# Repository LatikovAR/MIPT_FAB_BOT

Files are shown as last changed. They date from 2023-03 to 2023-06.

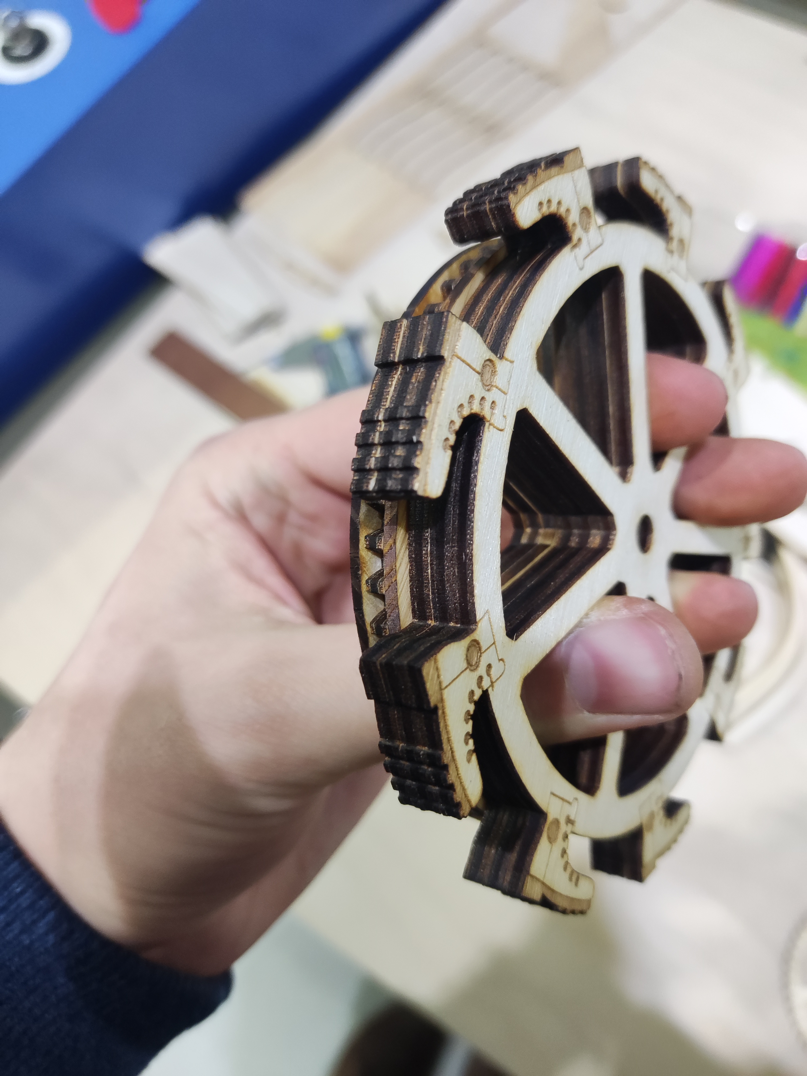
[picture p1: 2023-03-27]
Photo/laser1.jpg

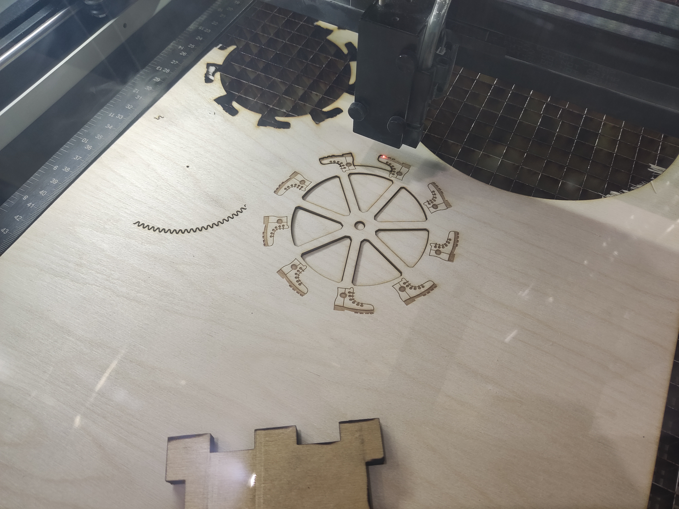
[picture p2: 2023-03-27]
Photo/laser0.jpg

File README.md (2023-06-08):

# MIPT_FAB_BOT

# Задача

Разработать передвигающегося робота для преодоления полосы препятствий, включающей (в порядке прохождения):
* Бассейн с зефирками
* Эстакаду
* Проезд по тунелю, выход из которого открывается светом
* Лопанье шарика.

Робот не должен быть гусеничным или иметь *абсолютно* круглые колеса. Приветствуется сделать максимально интересного робота.

# Решение

Шагающие машины, несмотря на их интересность, были отвергнуты из-за их сложности в изготовлении и отсутствие гарантии успешного решения задачи в условиях ограниченного времени.

В ходе планирования КБ "Инвалид" было принято реализовать классическую, надежную как швейцарские часы схему с полным приводом, двумя двигателями (по одному на 2 колеса каждой стороны) и жестко закрепленными колесами - поворот осуществляется разностью скоростей на правой и левой стороне.

engines

Для преодоления бассейна требовалась большая устойчивость и проходимость. Поэтому центр тяжести был опущен переносом аккумуляторов под днище и установкой больших колес для увеличения дорожного просвета, передаточное отношение двигатель-колесо 1:3.

Колеса из нескольких слоев 3мм фанеры с сапогами на ободе, отсюда одно из рабочих названий - "Пошло поехало". В роли полуосей выступают болты М5. Слоеное колесо зажимается гайками на полуоси. Крепление колес к кузову напечатано на 3D принтере, полуоси в нем фиксируются контргайками так, чтобы свободно вращаться.

Ведомые шестерни располагаются на колесах и зажаты дисками с обеих сторон. Диски фиксируют ведущую шестерню и исключают ее боковые перемещения. Ведущая шестерня вообще говоря может перемещаться по валу двигателя, но держится плотно.

wheels

Для увеличения жесткости, кузов сделан двухслойным, верхний слой стоит на стойках на расстоянии от днища. Напечатать стойки не получилось, они были заменены на набор вырезанных из фанеры шайб.

stoyka

Для открытия туннеля были реализованы огни на светодиодных лентах. А именно: автоматические поворотники и тормозные огни, габариты, включающиеся с пульта фары.

Пульт был собран на макетной плате, без корпуса. Управление осуществлялось двумя джойстиками, каждый управлял "газом" со своей стороны. Нажатия на джойстики активировали фары и пушку.



Пробитие шарика осуществлялось пушкой. Конструкция основана на таковой у страйкбольных приводов: шестерня с отсутствующими зубьями оттягивает подрезиненную рейку пока зубья не закончатся, после чего рейка отстреливает. На конце рейки закреплено лезвие. В результате испытаний оказалось что PLA не выдерживает таких ударных нагрузок, рейку разрывает и ее кусок отстреливает вместе с лезвием, что добавляет эффектности и поражающей способности. Поэтому рейка была склеена для единственного реального выстрела, с чем справилась.

Крепилась пушка стяжкой из-за нехватки времени. На случай отказа к передней части робота была прикреплена спица из проволоки.

bfg

knife

# Оборудование и материалы
* Arduino UNO x2 - пульт и "мозги" машины
* Сервопривод постоянного вращения FS5103R - привод шестерни пушки
* Коллекторные двигатели x2 - привод колес
* Motor shield - подключение коллекторных двигателей
* 2x 18650 с блоком - питание
* Адресная светодиодная лента WS281X - огни
* Радио модуль NRF24L01 - передача и прием сигнала
* 3D принтер Creality Ender-3 S1 Pro + PLA - печать креплений колес и двигателей, пушки
* GCC Laser Pro Spirit GLS 4.10 - лазерная резка 3мм фанеры: колеса и корпус.
* Болты M5 - полуоси
* Болты M3x8, M3x50 - крепление двигателей, корпуса, аккумуляторного блока, сборка пушки.

* Freecad, Solidworks - проектирование деталей под 3D печать
* CorelDraw, Inkscape - проектирование деталей под лазерную резку.

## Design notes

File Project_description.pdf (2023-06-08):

# Квадрокоптер своими руками

### Команда: Титов Егор Михайлович Латиков Александр Романович

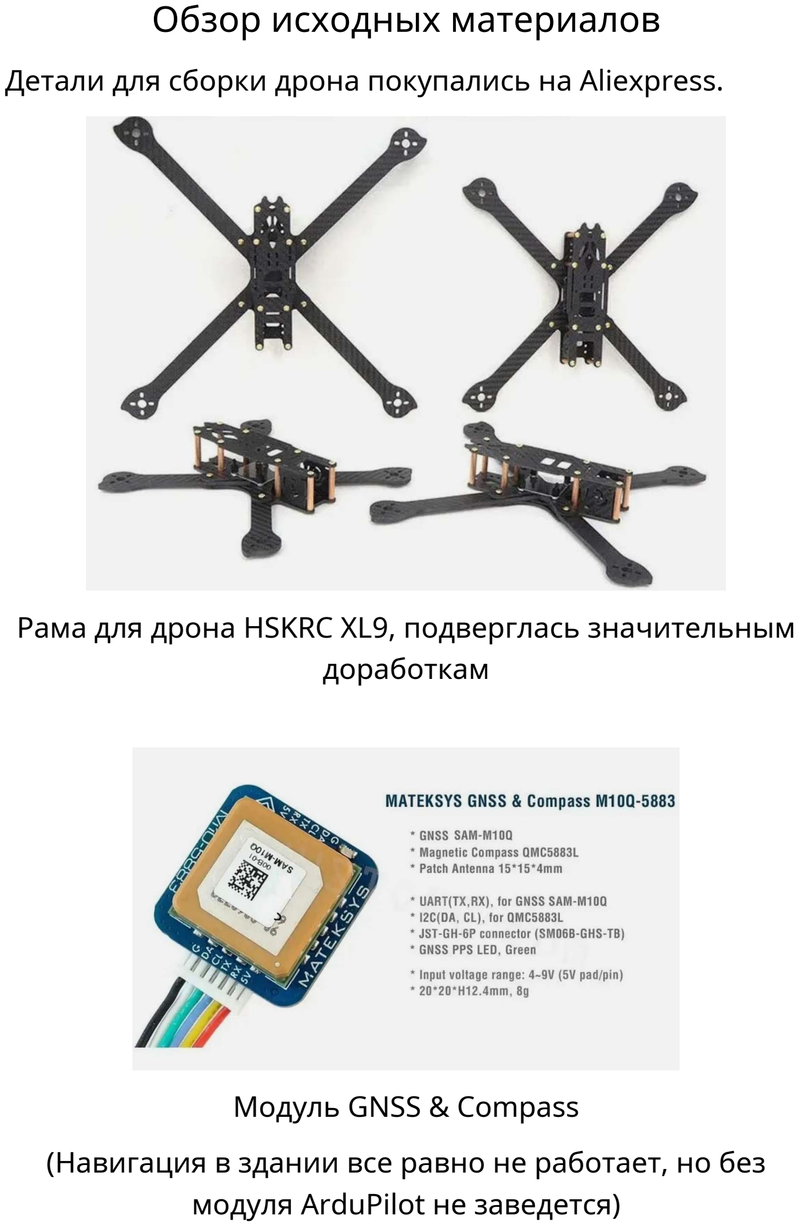
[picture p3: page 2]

### Обзор исходных материалов

Детали для сборки дрона покупались на Aliexpress.

Рама для дрона HSKRC XL9, подверглась значительным доработкам

Модуль GNSS & Compass
(Навигация в здании все равно не работает, но без модуля ArduPilot не заведется)

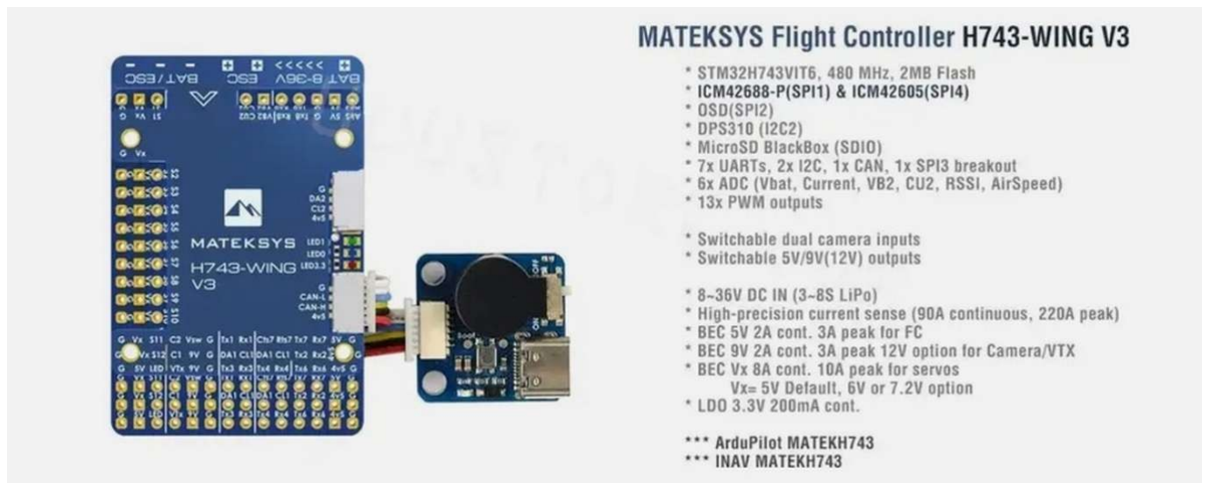
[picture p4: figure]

Полетный контроллер с программатором

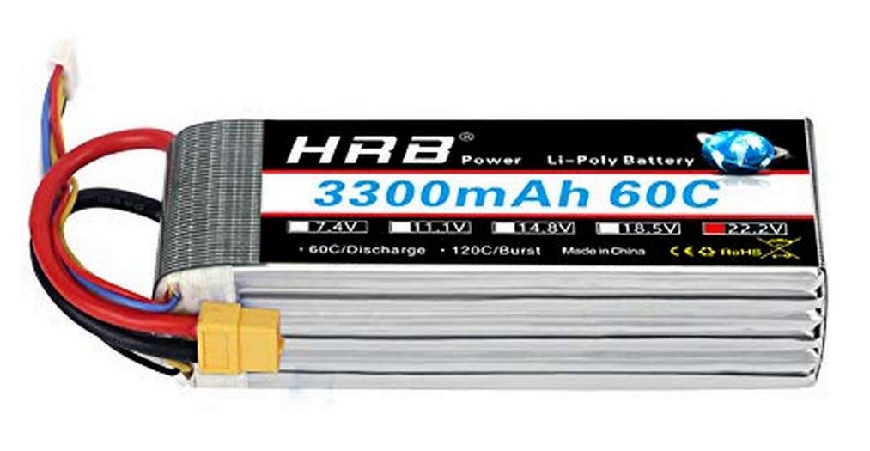
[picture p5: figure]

Аккумулятор HRB Lipo 4S 3300mah 60C XT60

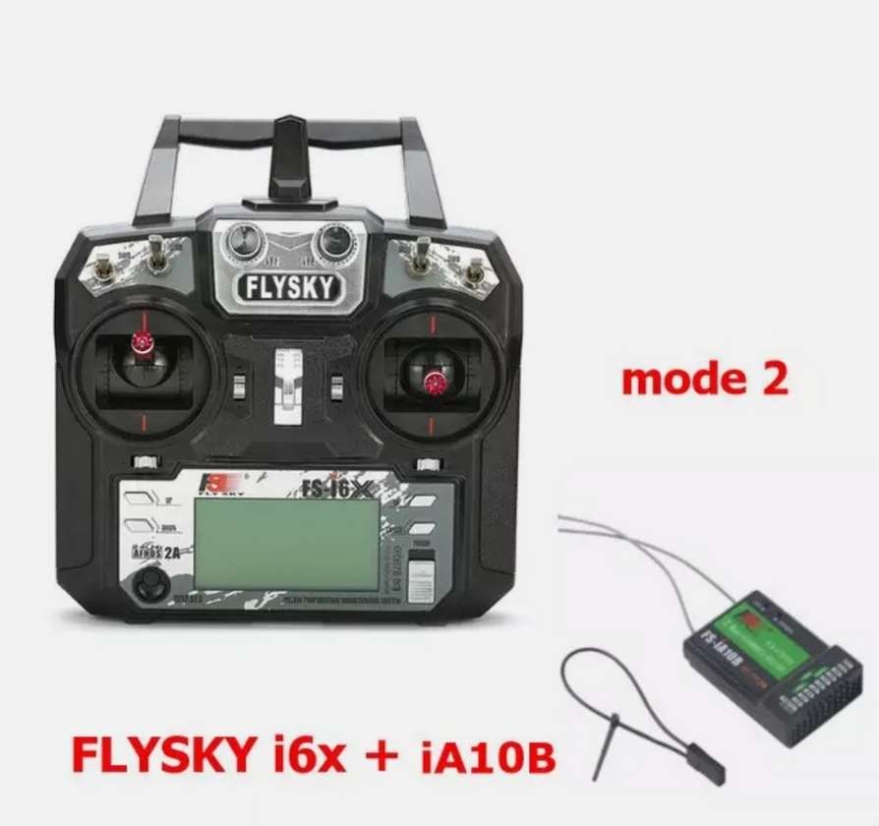
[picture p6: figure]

Передатчик + приемник управляющего сигнала Передатчик 10-канальный, на 2,4 ГГц Приемник 6-канальный, на 2,4 ГГц

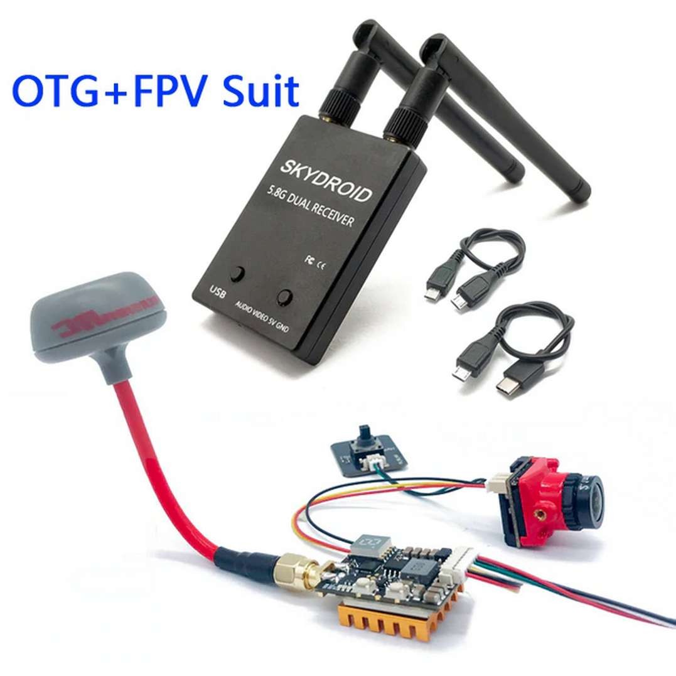
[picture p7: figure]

FPV система
аналоговая камера
передатчик + приемник 5.8 ГГц

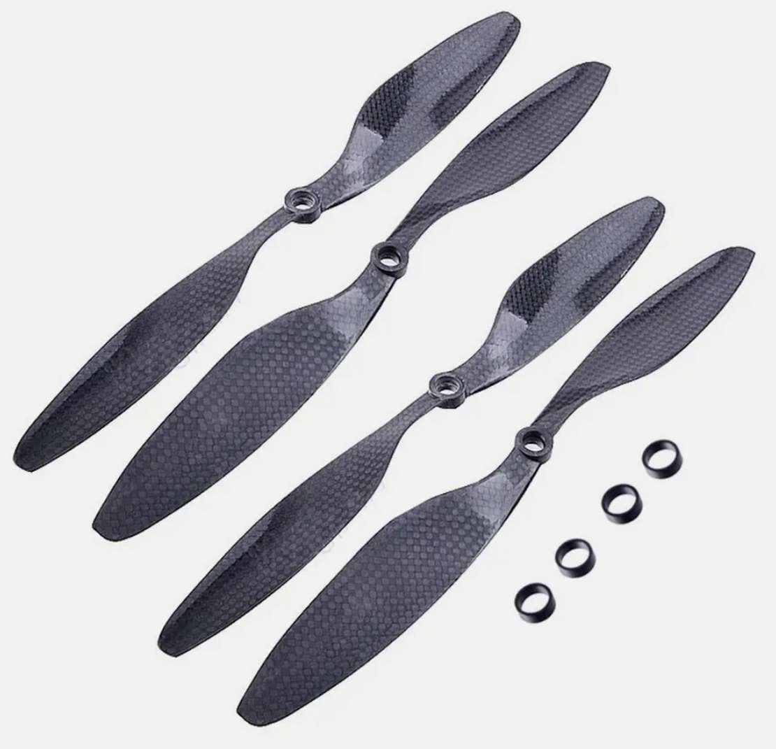
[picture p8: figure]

Комплект пропеллеров 1

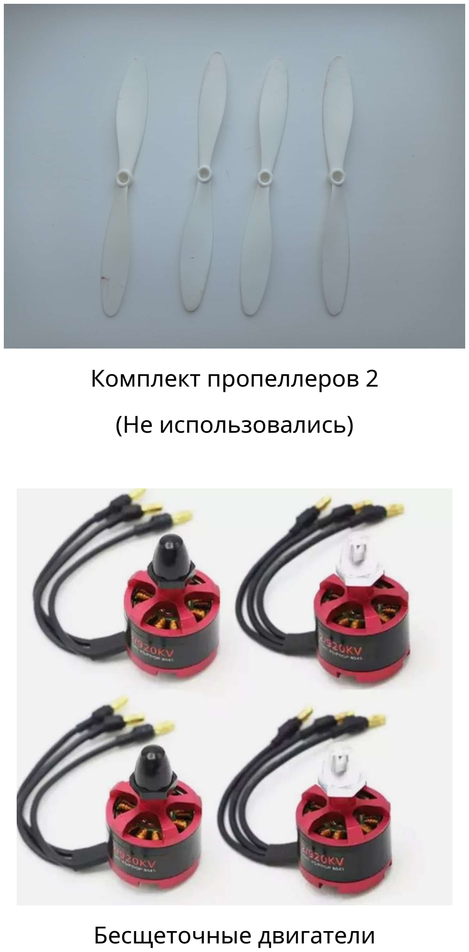
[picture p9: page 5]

Комплект пропеллеров 2
(Не использовались)

Бесщеточные двигатели

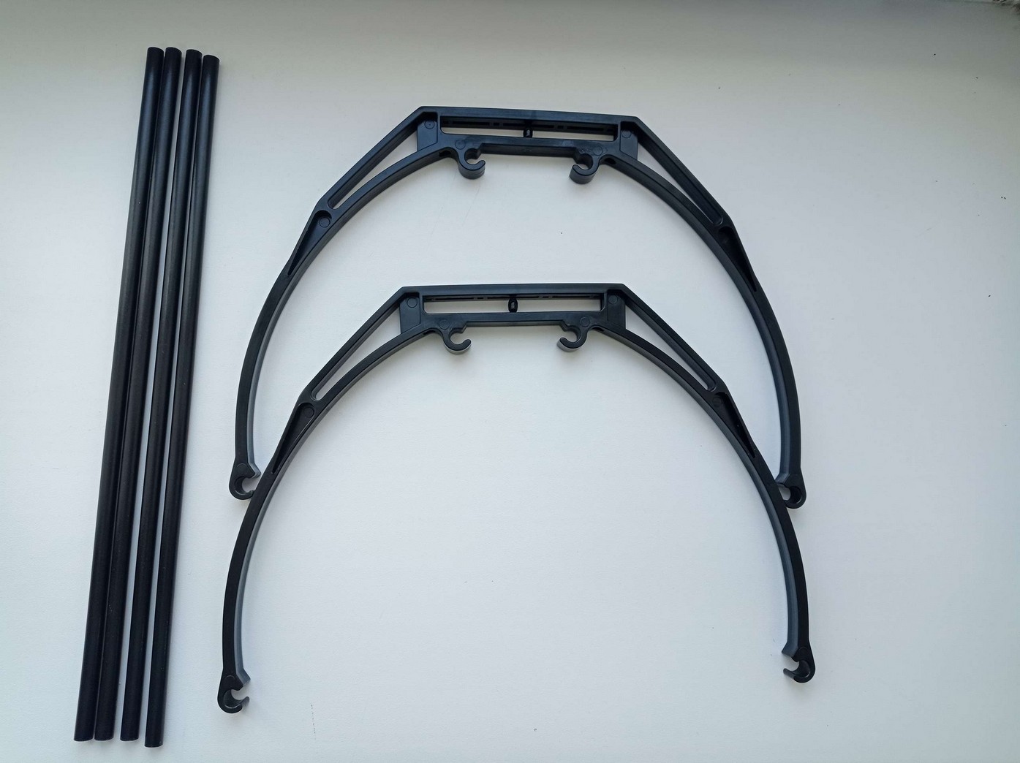
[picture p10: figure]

Шасси
(Использовались только углепластиковые трубки)

### Держатель для камеры

В комплекте рамы были приспособления для закрепления камеры.

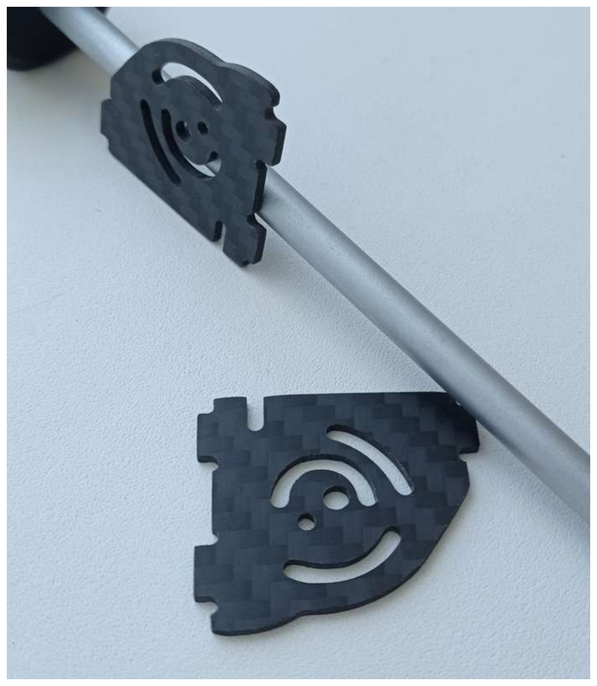
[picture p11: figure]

Однако в силу своей геометрии они не подходили к нашей камере. Поэтому для них была сделана замена:

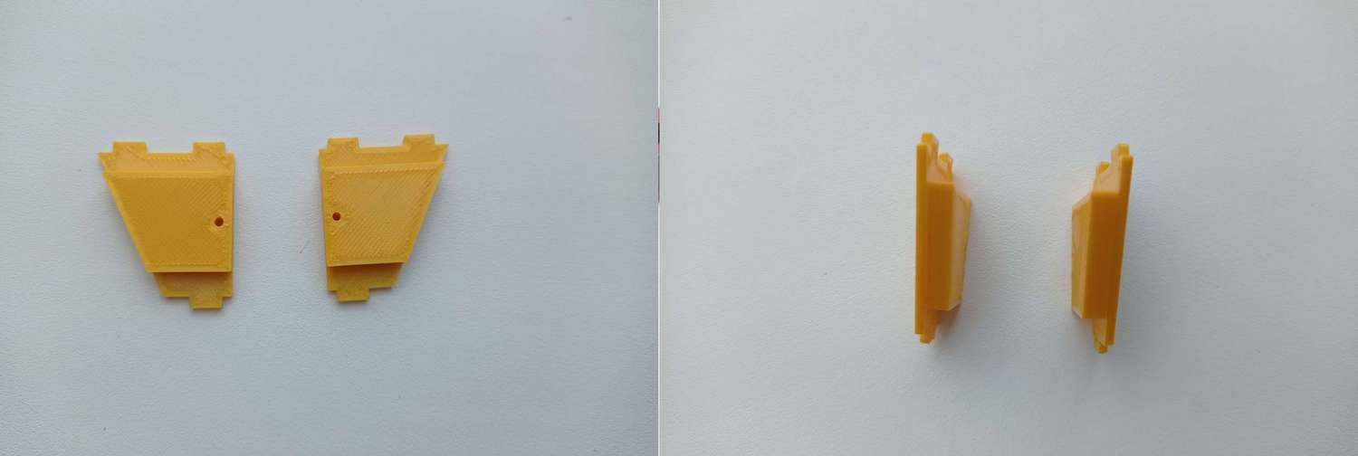
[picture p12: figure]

### Стойки для антенн

Для закрепления антенн приема управляющего сигнала, передачи видеоизображения и антенны GNSS были изготовлены стойки. При их разработке ставилась задача максимально возможного удаления антенн друг от друга для снижения возможного взаимного влияния.

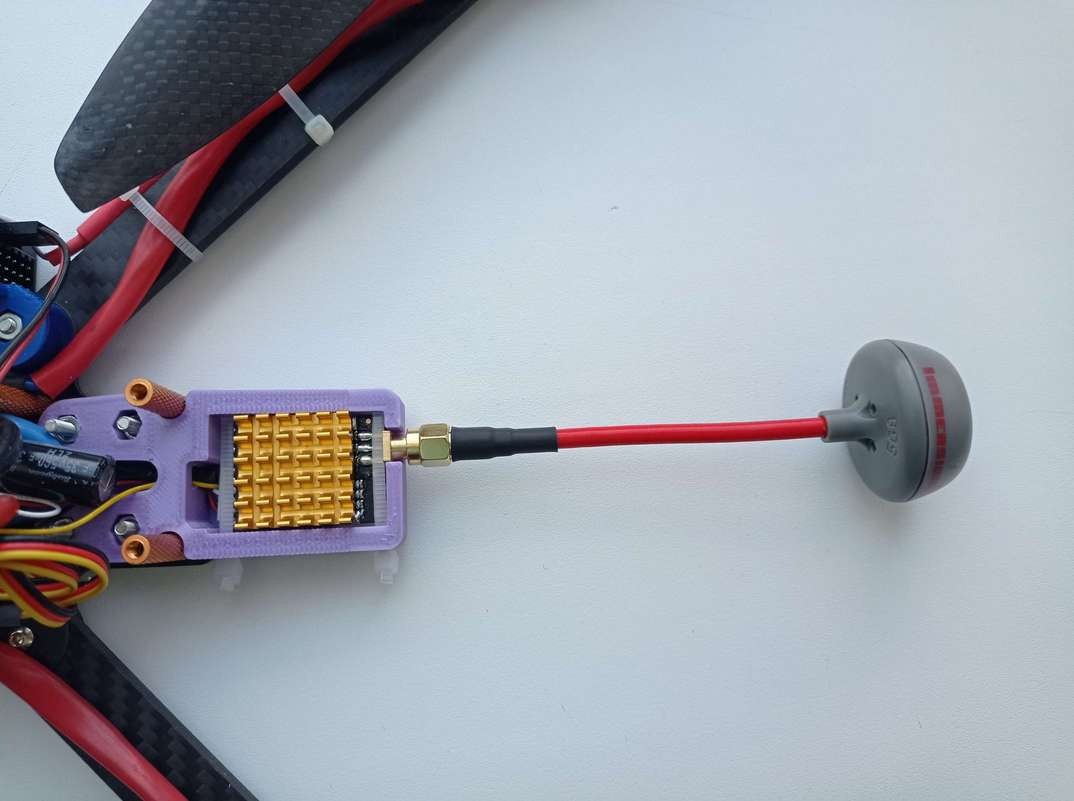
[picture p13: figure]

Передатчик видеоизображения

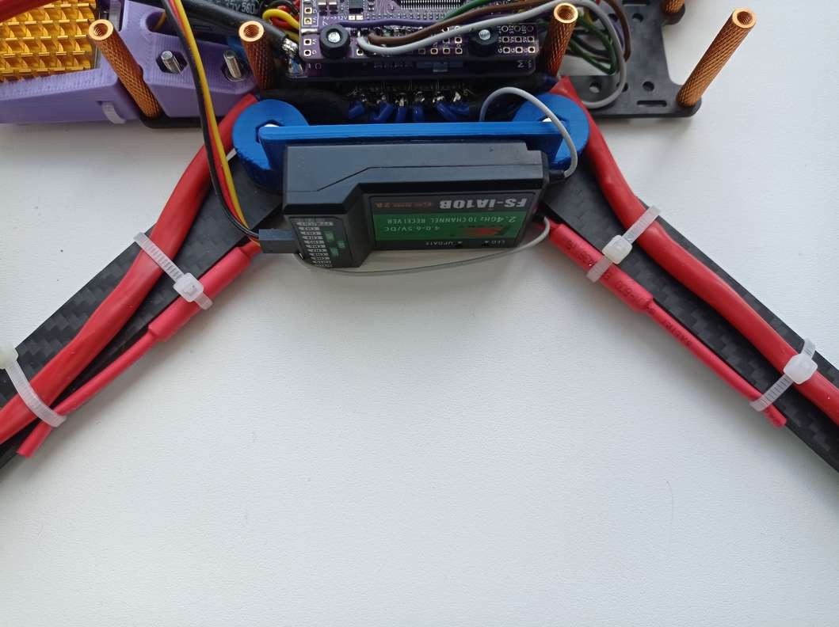
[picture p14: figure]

Приемник управляющего сигнала (Сами антенны закреплены стяжками на раму)

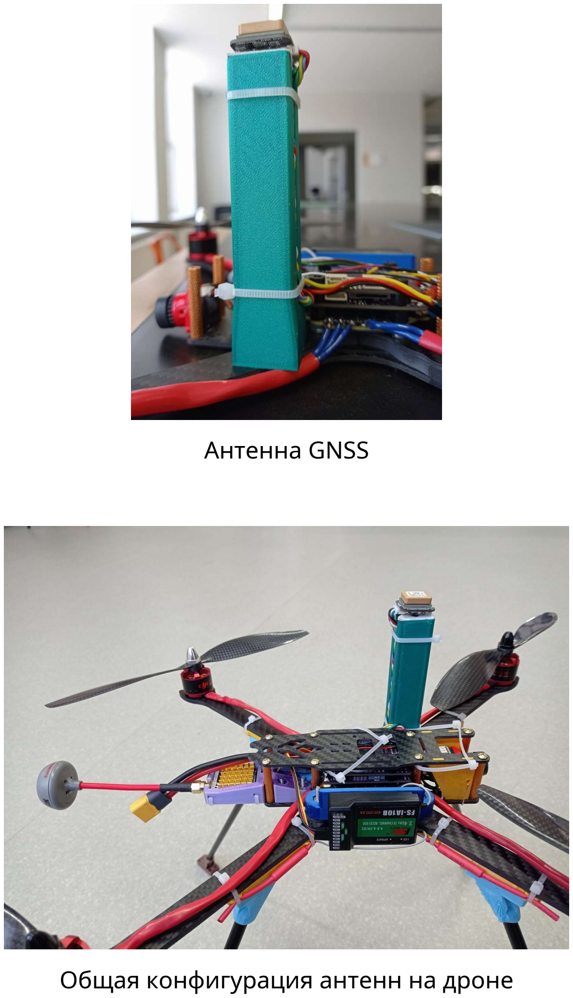
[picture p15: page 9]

Антенна GNSS

Общая конфигурация антенн на дроне

### Сопряжение лопастей и двигателей

Имеющиеся двигатели и лопасти не подходили друг к другу. Большой проблемой было то, что диаметр отверстия лопасти был больше диаметра вала двигателя на ~0.2мм. Сделать втулку под такие размеры крайне проблематично. После исследования различных вариантов для ликвидации зазора была выбрана термоусадка. Процесс установки лопастей является относительно трудоемким для повторения и не был отснят, поэтому подробной фотографии нет.

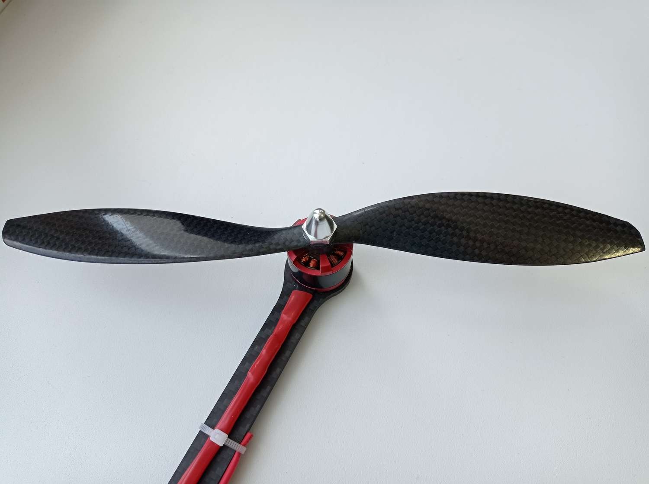
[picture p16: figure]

### Разводка и пайка электроники

Довольно трудоемким был процесс разводки и пайки проводов для соединения компонентов между собой. Основную сложность составляли очень ограниченные размеры и геометрия, диктуемые рамой беспилотника.

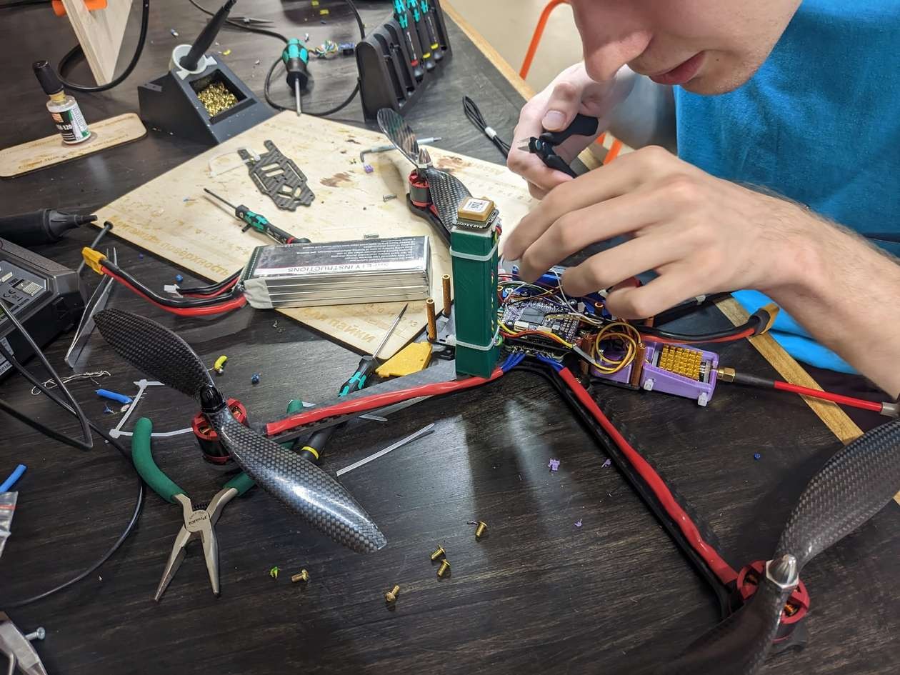
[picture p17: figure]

Процесс распайки

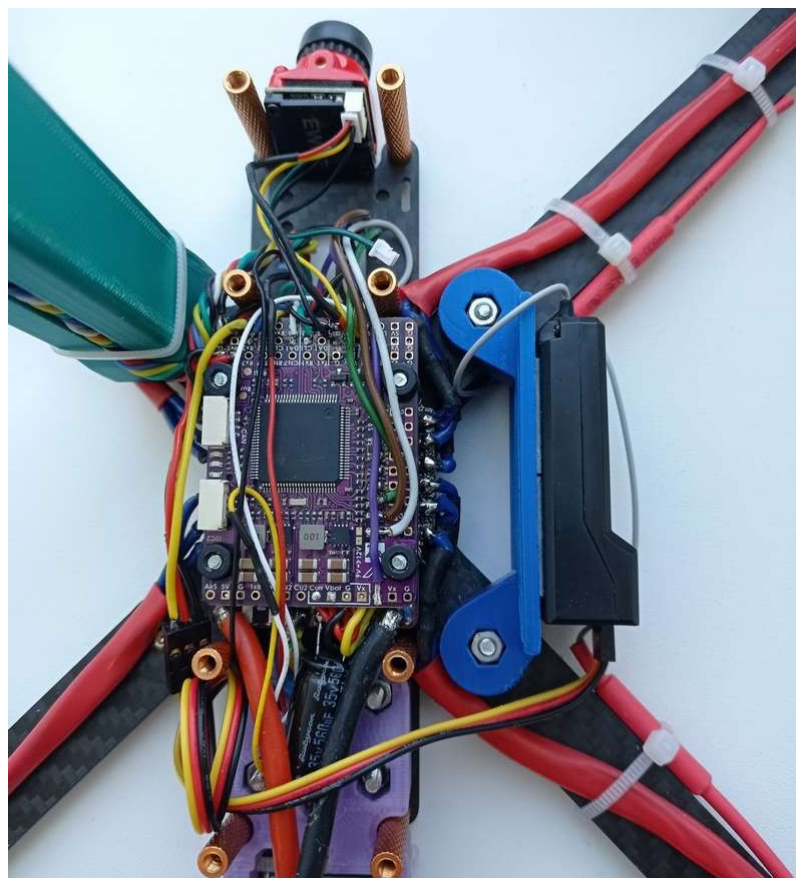
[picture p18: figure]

Результат

### Программная часть

В качестве прошивки используется Ardupilot c открытым исходным кодом. Ardupilot поддерживает используемый полетный контроллер, потребовалось только прошить бинарный файл во внутреннюю память.
Ardupilot работает в паре с компьютерным ПО для настройки. Мы использовали MissionPlanner.

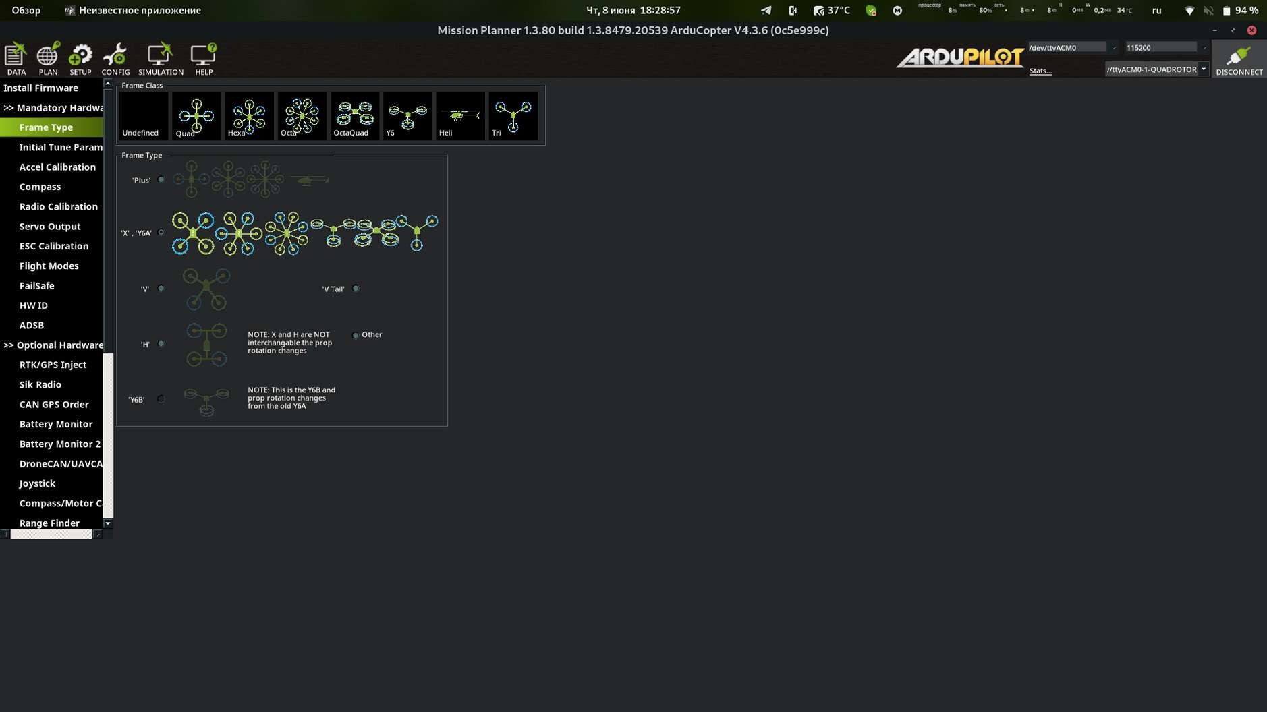
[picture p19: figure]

Ardupilot имеет подробную документацию к настройкам и инструкции. Настройку можно производить в отведенных секциях или в сводной таблице параметров (там мы отключали логгирование т. к. иначе невозможен запуск без sd карты).

В пульте потребовалось инвертировать 2й канал т. к. движение вперед-назад было инвертировано.

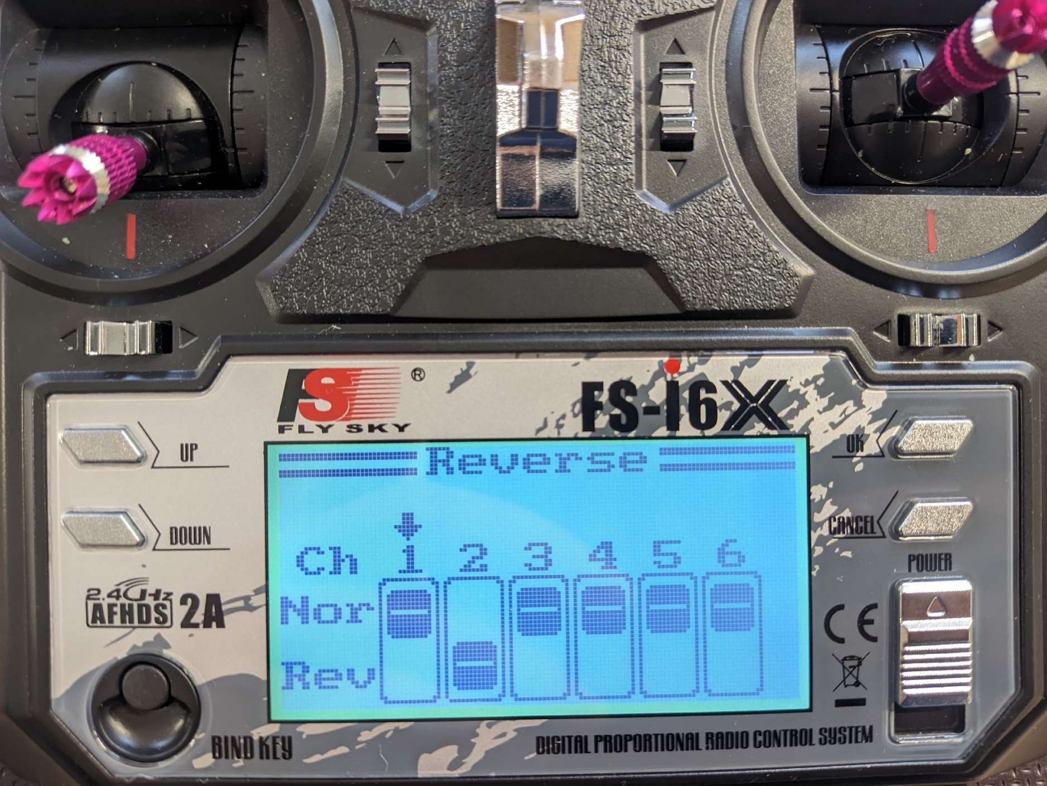
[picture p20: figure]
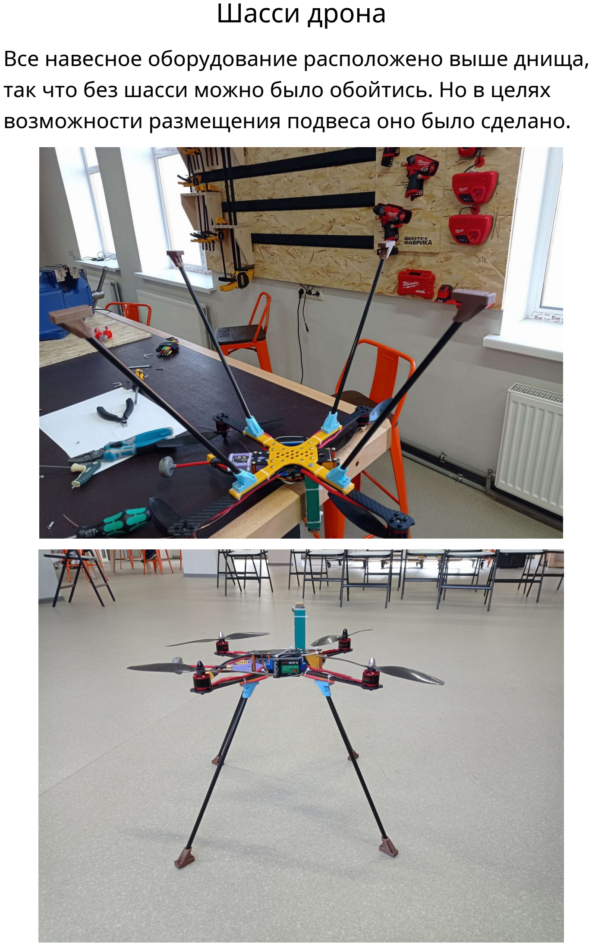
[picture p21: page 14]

### Шасси дрона

Все навесное оборудование расположено выше днища, так что без шасси можно было обойтись. Но в целях возможности размещения подвеса оно было сделано.

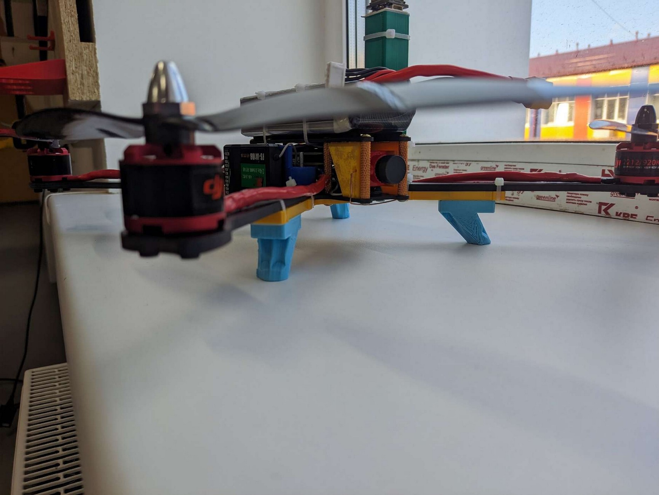
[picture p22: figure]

Шасси съемное

### Описание существующих аналогов

В настоящее время существует огромное количество разнообразных моделей дронов. Некоторые из них выпускаются серийно, многие являются любительскими моделями.
Нашей целью было создать рабочую модель из тех материалов, которые были у нас в наличии. Мы не стремились достичь каких-либо выдающихся характеристик или особого функционала, так как понимали, что это нам не по силам при текущем уровне развития и допустимых затратах времени. Мы не стремились сделать модель для коммерческого производства, так как понимали бесперспективность этого занятия при наших ресурсах.

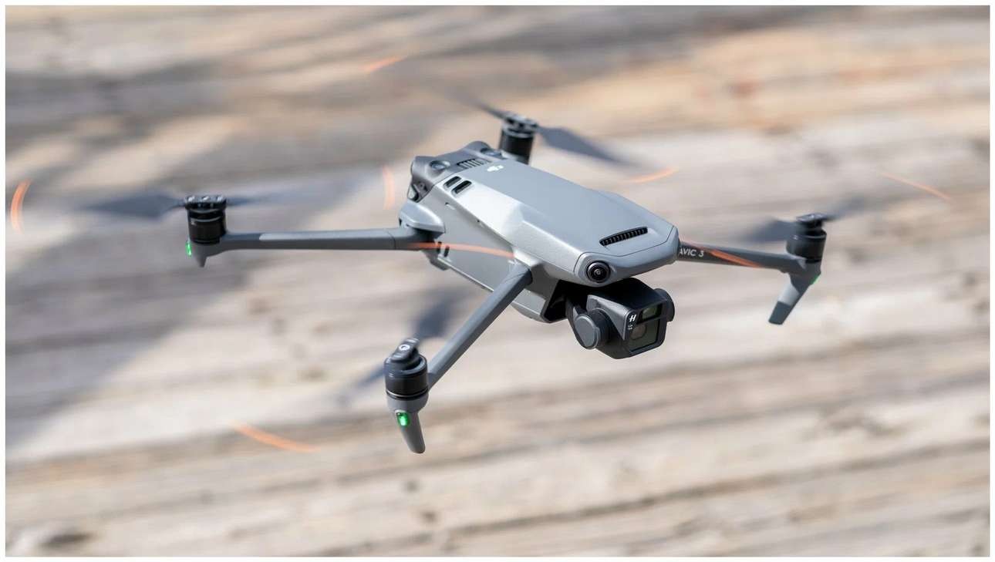
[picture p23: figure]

Дрон DJI Mavic

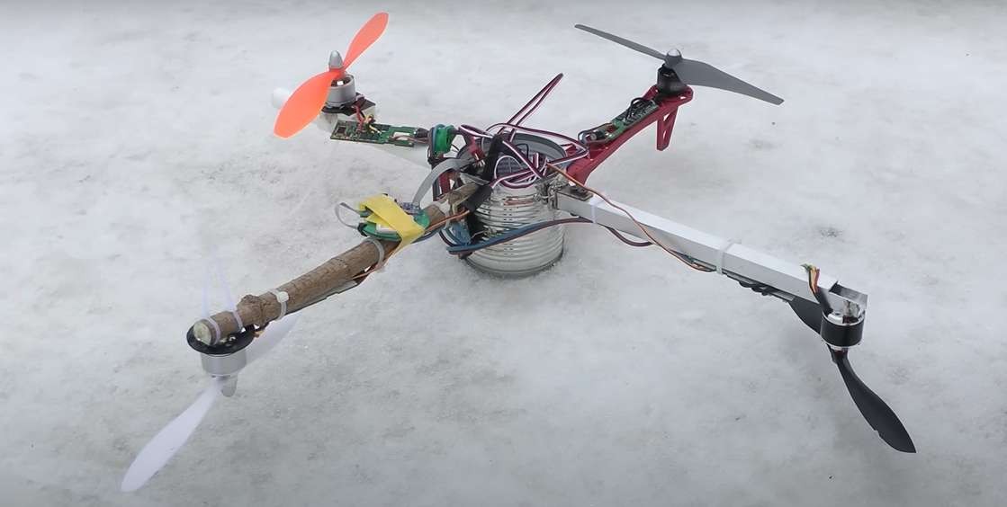
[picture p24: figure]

Проект хламолет
(у нас не настолько подручные материалы)

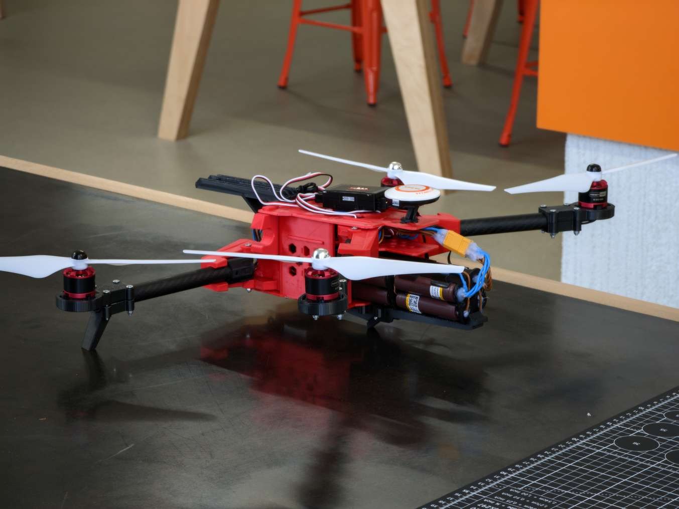
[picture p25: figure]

Дрон от другой команды

### Личный вклад членов команды

Исходные материалы - нашлись у Егора Держатель камеры - Александр
Стойки для антенн - Егор
Сопряжение лопастей и двигателей - Александр Сборка рамы - коллективная
Разводка и пайка электроники - коллективная Настройка ArduPilot - Егор
Подставка - Егор
Создание отчета - Александр

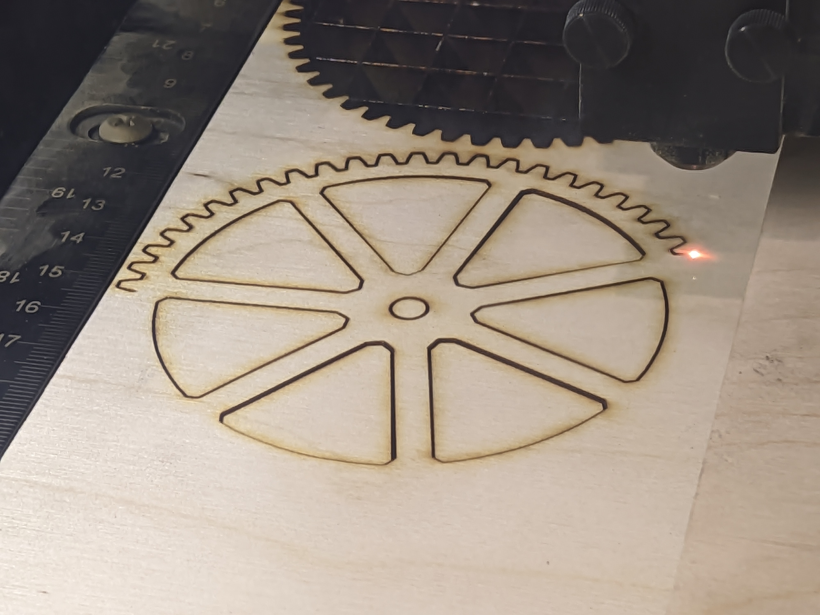
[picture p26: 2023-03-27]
Photo/laser2.jpg

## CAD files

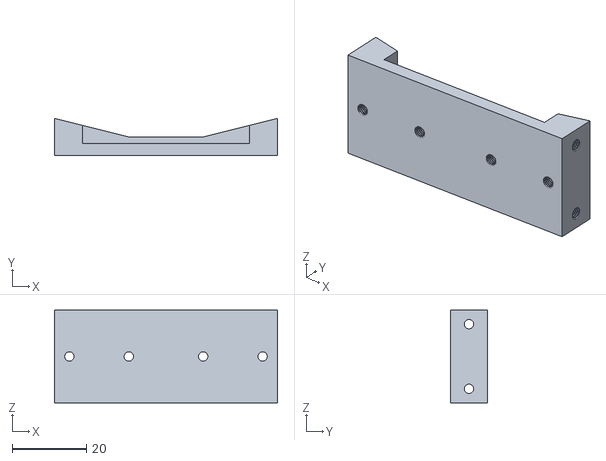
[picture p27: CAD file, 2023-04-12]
drafts/bech-BodyHole001.stl
60.0 x 10.0 x 25.0

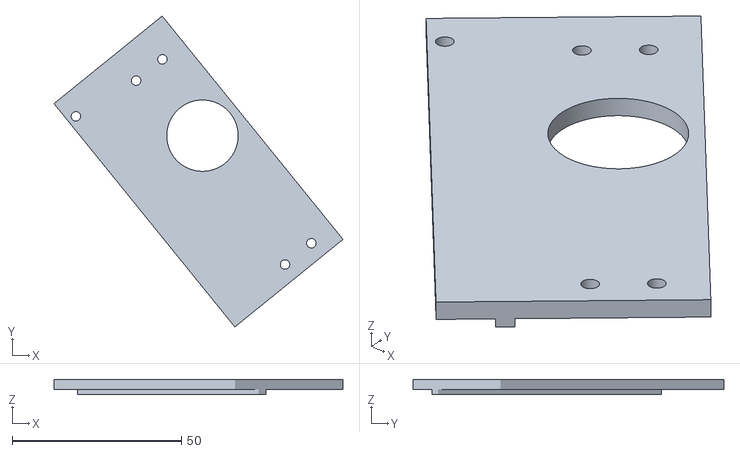
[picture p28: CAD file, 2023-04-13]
drafts/drive/drive-case-motor.stl
85.5 x 92.0 x 4.40

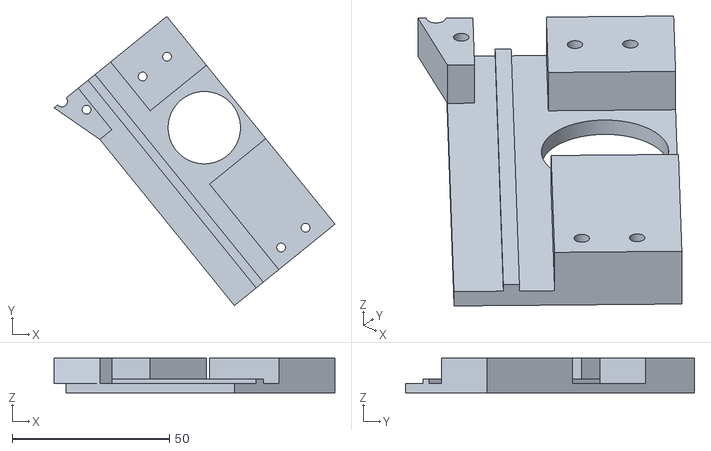
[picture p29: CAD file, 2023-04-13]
drafts/drive/drive-case-no-motor.stl
89.4 x 92.0 x 11.0

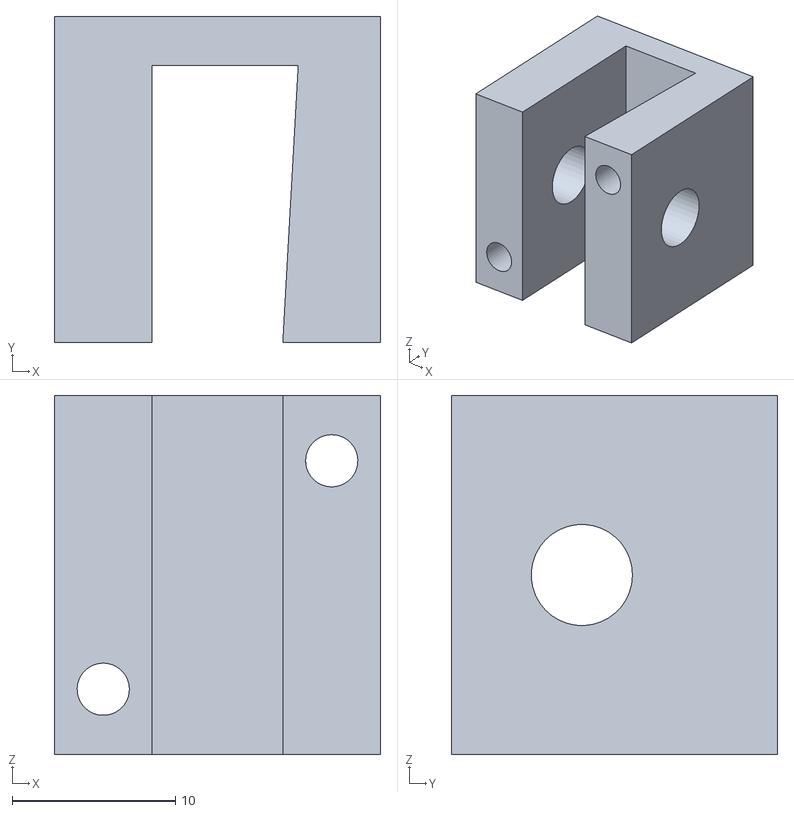
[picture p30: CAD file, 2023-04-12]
drafts/Part1.STL
20.0 x 20.0 x 22.0

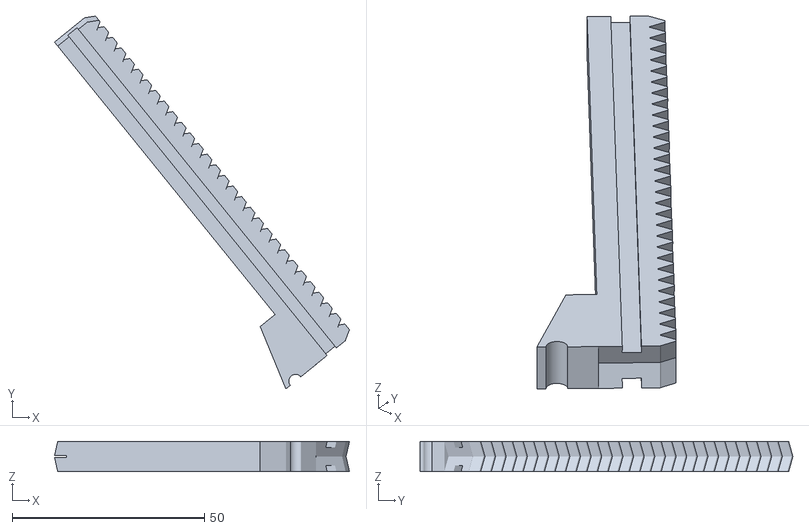
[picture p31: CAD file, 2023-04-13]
drafts/drive/drive-rack.stl
76.6 x 96.9 x 7.80

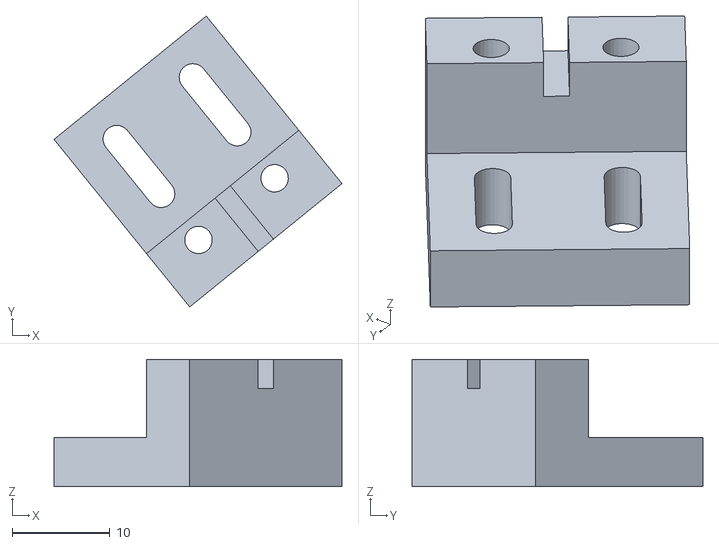
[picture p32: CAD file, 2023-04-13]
drafts/drive/drive-motor-bench-x2.stl
29.4 x 29.7 x 13.0

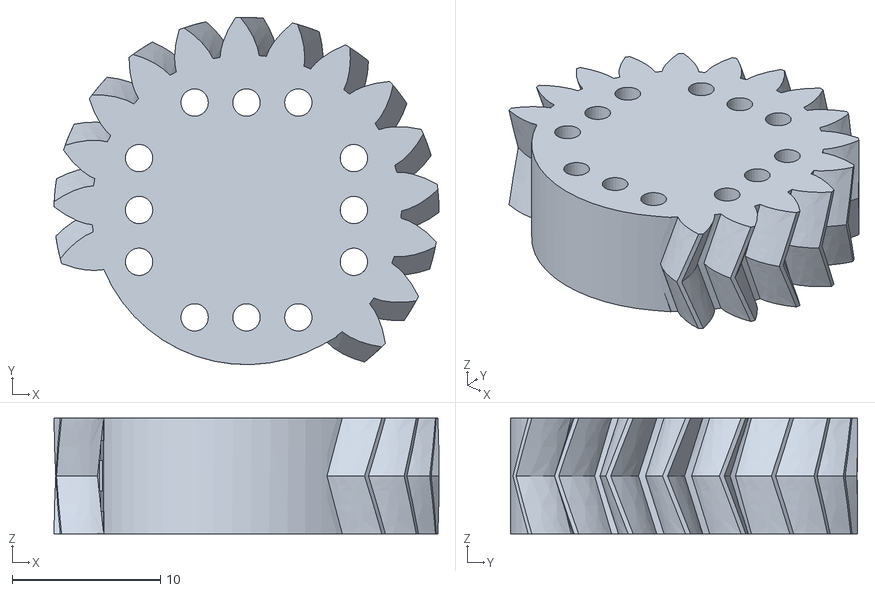
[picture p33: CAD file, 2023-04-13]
drafts/drive/drive-gear.stl
26.0 x 23.4 x 7.80

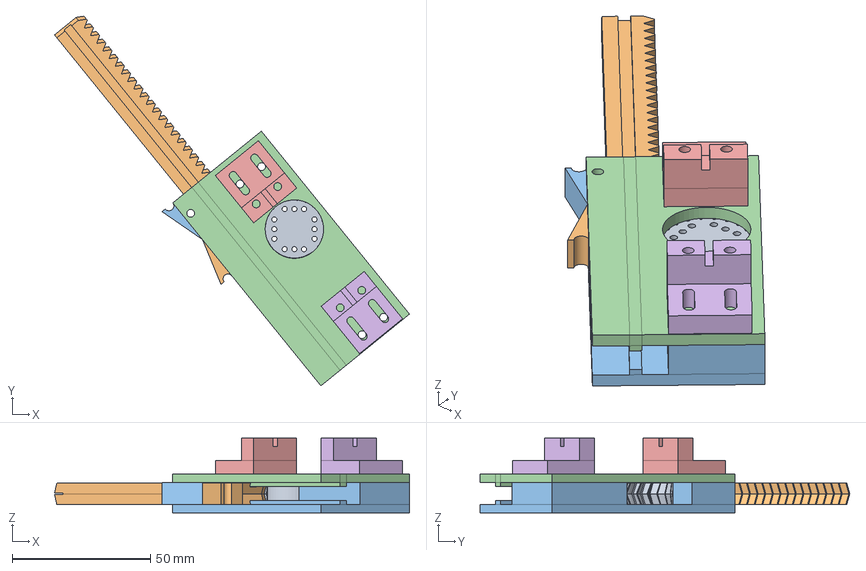
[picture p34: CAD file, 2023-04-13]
drafts/drive/drive.FCStd
128.2 x 133.5 x 27.0 mm
Gear
Rack
Case-no-motor
Case-motor
Motor-bench0
Motor-bench1

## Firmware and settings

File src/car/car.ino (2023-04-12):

#include <SPI.h>  // Подключаем библиотеку для работы с SPI-интерфейсом
#include <nRF24L01.h> // Подключаем файл конфигурации из библиотеки RF24
#include <RF24.h> // Подключаем библиотеку для работа для работы с модулем NRF24L01
#include <microLED.h>

#define PIN_CE  2  // Номер пина Arduino, к которому подключен вывод CE радиомодуля
#define PIN_CSN 3 // Номер пина Arduino, к которому подключен вывод CSN радиомодуля
#define DIRM1 4 // Направление M1
#define  SPEEDM1 5
#define DIRM2 7
#define SPEEDM2 6
#define MUX 1
#define HIGH_LEVEL_LEFT 512
#define LOW_LEVEL_LEFT 465
#define HIGH_LEVEL_RIGHT 550
#define LOW_LEVEL_RIGHT 500
#define LED 10
#define NUMLEDS 5     // кол-во светодиодов

RF24 radio(PIN_CE, PIN_CSN); // Создаём объект radio с указанием выводов CE и CSN

microLED <NUMLEDS, LED, -1, LED_WS2813, ORDER_GRB> leds;

int potValue[3]; // Создаём массив для приёма значений потенциометра

void setup() {
  pinMode(DIRM1, OUTPUT);
  pinMode(DIRM2, OUTPUT);
  pinMode(SPEEDM1, OUTPUT);
  pinMode(SPEEDM2, OUTPUT);
  radio.begin();  // Инициализация модуля NRF24L01
  radio.setChannel(44); // Обмен данными будет вестись на пятом канале (2,405 ГГц)
  radio.setDataRate (RF24_1MBPS); // Скорость обмена данными 1 Мбит/сек
  radio.setPALevel(RF24_PA_HIGH); // Выбираем высокую мощность передатчика (-6dBm)
  radio.openReadingPipe(1, 0x787); // Открываем трубу ID передатчика
  radio.startListening(); // Начинаем прослушивать открываемую труб
  leds.setBrightness(255);  // яркость
  Serial.begin(9600);
}

void loop() {
  static volatile unsigned long millis_off_prev = 0;
  if(radio.available()){
    millis_off_prev = millis();
    leds.set (0, mRGB(255, 255, 255));
    leds.set (NUMLEDS-1, mRGB(255, 255, 255));
    radio.read(potValue, 6);
    Serial.print(potValue[0]);
    Serial.print("\t");
    Serial.print(potValue[1]);
    Serial.print("\t");
    Serial.print(potValue[2]);
    Serial.print("\n");
    if (potValue[2]) {
      for (byte i = 1; i < NUMLEDS - 1; i++) {
        leds.set (i, mRGB(255, 200, 0));
      }
    }
    else {
      for (byte i = 1; i < NUMLEDS - 1; i++) {
        leds.set (i, mRGB(0, 0, 0));
      }
    }
    // Если в буфер приёмника поступили данные
    if (((potValue[0] < LOW_LEVEL_LEFT) | (potValue[0] > HIGH_LEVEL_LEFT))){
      if (potValue[0] < LOW_LEVEL_LEFT){
        digitalWrite(DIRM1, HIGH);
        analogWrite(SPEEDM1, (LOW_LEVEL_LEFT - potValue[0])/2);
      }
       else{
            digitalWrite(DIRM1, LOW);
         analogWrite(SPEEDM1, (potValue[0] - HIGH_LEVEL_LEFT)/2);
      }
    }
    else{
      analogWrite(SPEEDM1,0);
    }
    if (((potValue[1] < LOW_LEVEL_RIGHT) | (potValue[1] > HIGH_LEVEL_RIGHT))){
      if (potValue[1] < 500){
        digitalWrite(DIRM2, HIGH);
       analogWrite(SPEEDM2, (LOW_LEVEL_RIGHT - potValue[1])/2);
      }
      else{ 
        digitalWrite(DIRM2, LOW);
        analogWrite(SPEEDM2, (potValue[1] - HIGH_LEVEL_RIGHT)/2);
      }
    }
    else{
      analogWrite(SPEEDM2,0);
    }
  }
  else {
    Serial.println ("radio not avail");
    if (millis () - millis_off_prev > 1000) {
      for (byte i = 0; i < NUMLEDS; i++) {
        leds.set (i, mRGB(0, 0, 0));
      }
      millis_off_prev = millis();
    }
  }
  static volatile unsigned long millis_prev = 0;
  if (millis () - millis_prev > 1) { // if 1ms passed
      leds.show();
      millis_prev = millis();
    }
}

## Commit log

2023-03-27 Added laser cutting process photos.
2023-04-12 added code and drafts
    [Part1.STL, bech-BodyHole001.stl]
2023-04-12 correct segment owerflow, front leds working good.
    [car.ino, remote.ino]
2023-04-13 added drive model
    [drive-case-motor.stl, drive-case-no-motor.stl, drive-gear.stl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]
